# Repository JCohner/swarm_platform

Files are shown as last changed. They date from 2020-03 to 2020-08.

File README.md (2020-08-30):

# Swarm Robotic Platform
### Josh Cohen

## Intro
With the goal of making decentralized, equitable, and sustainable systems, swarm robotic systems seem like a promising framework. Inspired by the success of the open source hardware community over the past 10 years and works like the [swarmbot: Jasmine](http://www.swarmrobot.org/), I hope to attempt to design my own low cost platform that can help propel swarm robotics into the real world. 




## TI CC1310
This is the [micro-conrtoller](http://www.ti.com/product/CC1310) we are using due to its small profile, low power consumption, and integrated RF capabilities. This board is currently interfacing with a [Pololu Zumo](https://www.pololu.com/product/2508) robot through a custom connector board.    

## Current Work
* Working "Firefly Synchronicity" inspired biosynchronicity algorithm that multiplexes time domain such that all robots can communicate within a given time period (\~1 second)
* 2 Working PCB Implementations:
	* Interface to Zumo Robot and CC13310 Launchpad XL
	* From scrath PCB for the CC1310 with working integrated PCB RF Antena that also serves as chassis for a diff drive robot
* Working line following robot that communcites based on the "Bayesian Particle" control laws researched by Ana Pervan and the Murphy lab
	* bit wise state machine to handle state transitions between every encountered intersection

## Directory Structure
* cc1310_code
	code running on the CC1310, controls zumo, implements RF synchronicity algorithm. See directory for more information
* listener
	* code that runs on "Hub" zumo, intercepts all TX'd messages from the zumo cc1310s and interperts the packets to be transmitted on via serial to the host computer, must also be used to communicate to zumos that start|stop them running or change their policies.  
* doc
	documentation relating to the Zumo, CC1310, and other components in this design
* eagle_files
	all PCB related documents
* scripts
	* a script to interpret and graph outputs of the ADC reads from the IR color sensors 
	* small c files in which we can test the bitwise state machine
* interface
	* hub.py is run to open the gui that lets you control the robots and collect data
* stls 
	* holds stl files for which the CAD can be found at [here](https://cad.onshape.com/documents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)

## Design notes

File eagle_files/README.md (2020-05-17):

##Board 2.0
Switched LM1117 voltage regs to constant output, 1 5v reg and one 3.3v output

## Board 1.0
Needs LM1117 to be adjustable

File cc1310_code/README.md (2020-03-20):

# Swarm Robotic Platform
### Josh Cohen

## Intro
With the goal of making decentralized, equitable, and sustainable systems, swarm robotic systems seem like a promising framework. Inspired by the success of the open source hardware community over the past 10 years and works like the [swarmbot: Jasmine](http://www.swarmrobot.org/), I hope to attempt to design my own low cost platform that can help propel swarm robotics into the real world. 

## TI CC1310
This is the [micro-conrtoller](http://www.ti.com/product/CC1310) we are using due to its small profile, low power consumption, and integrated RF capabilities. This board is currently interfacing with a [Pololu Zumo](https://www.pololu.com/product/2508) robot through a custom connector board.    

## Current Work
* Integrate biosynchronicity algorithm with Zumo movement to get them to "dance"
* Iterate on board
	* custom PCB for CC1310
	* LED array for representing bitwise memory
	* power at 3.3V  
* reorganize this github

## Accomplished Work
* Implemented driver library level functionality of control of the Zumo robot
* Designed v1.0 of interface PCB
* Implemented prototype of a custom biosynchronicity algorithm using the CC1310's RF Driver

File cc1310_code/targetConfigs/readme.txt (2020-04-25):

The 'targetConfigs' folder contains target-configuration (.ccxml) files, automatically generated based
on the device and connection settings specified in your project on the Properties > General page.

Please note that in automatic target-configuration management, changes to the project's device and/or
connection settings will either modify an existing or generate a new target-configuration file. Thus,
if you manually edit these auto-generated files, you may need to re-apply your changes. Alternatively,
you may create your own target-configuration file for this project and manage it manually. You can
always switch back to automatic target-configuration management by checking the "Manage the project's
target-configuration automatically" checkbox on the project's Properties > General page.

Josh Additions:
to find serial numbers use the xdsdfu tool found in ~/ti/ccs930/ccs/ccs_base/common/uscif/xds110

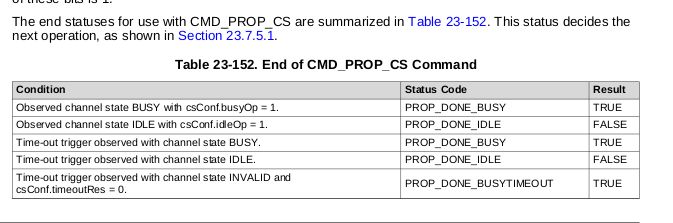
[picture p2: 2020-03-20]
doc/CC1310/RF_CS_return_vals.png

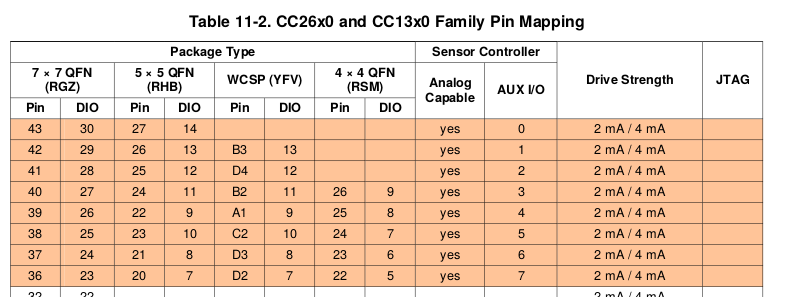
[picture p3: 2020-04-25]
doc/CC1310/helpful_images/IO_Pin__MAP_for_analog.png

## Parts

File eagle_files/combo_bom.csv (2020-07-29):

Part | Vendor | Quantity | Digi-Key Part Number | Customer Reference
10 Pos Male Header | 3M | 25 | 3M9457-10-ND | 10 Pos Male Head
10 Pos Female Header | Sullins Connector Solutions | 10 | S7008-ND | 10 Pos Female Header
8 Pos Female Header | Sullins Connector Solutions | 20 | S7006-ND | 8 Pos Female Header
6 Pos Female Header | Sullins Connector Solutions | 10 | S7004-ND | 6 Pos Female Header
 | Texas Instruments | 10 | LM1117MPX-5.0/NOPBCT-ND | LM1117 5V
 | Texas Instruments | 10 | LM1117MPX-3.3/NOPBCT-ND | LM1117 3v3
 | AVX Corporation | 20 | 478-9320-ND | 10 uF
 | AVX Corporation | 20 | 478-9333-ND | 100 uF
 | Stackpole Electronics Inc | 10 | CF14JT1K00CT-ND | 1k
 | Stackpole Electronics Inc | 50 | CF14JT330RCT-ND | 330
 | Stackpole Electronics Inc | 50 | S200QCT-ND | 220
 | Cree Inc. | 50 | C503B-BCN-CV0Z0462CT-ND | Blue LED
 | Cree Inc. | 50 | C503B-GAN-CB0F0792CT-ND | Green LED

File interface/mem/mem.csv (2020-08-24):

MAC | ser | status
20CE | LDO | 1
A3EB | LXP | 1
C464 | KDS | 1
A171 | M52 | 1
C262 | M4S | 1
A146 | M5X | 1
C683 | M4A | 1
B5A8 | M48 | 1
C219 | M4K | 1
C718 | CGV | 0

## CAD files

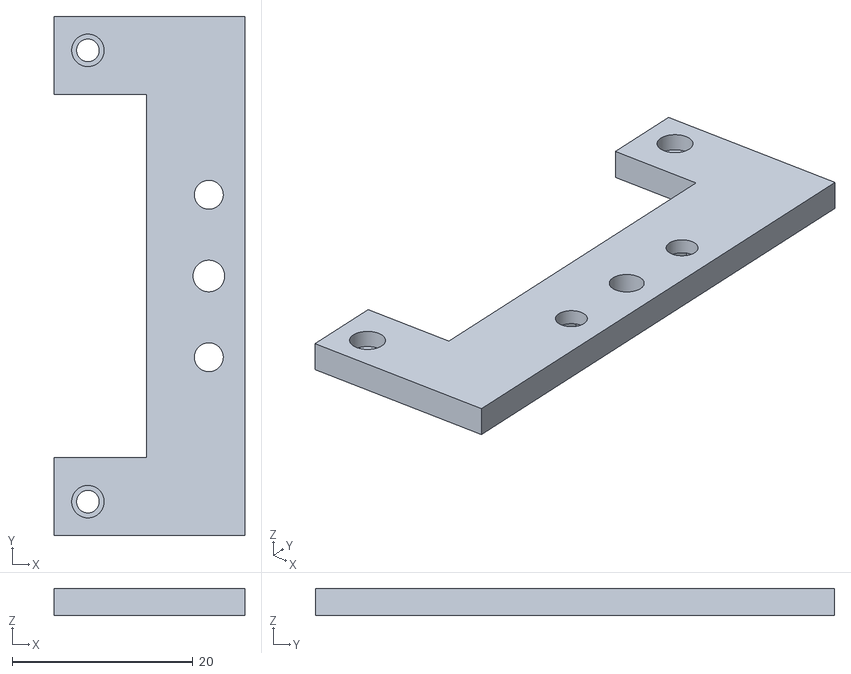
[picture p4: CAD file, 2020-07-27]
stls/front.stl
21.1 x 57.5 x 3.00

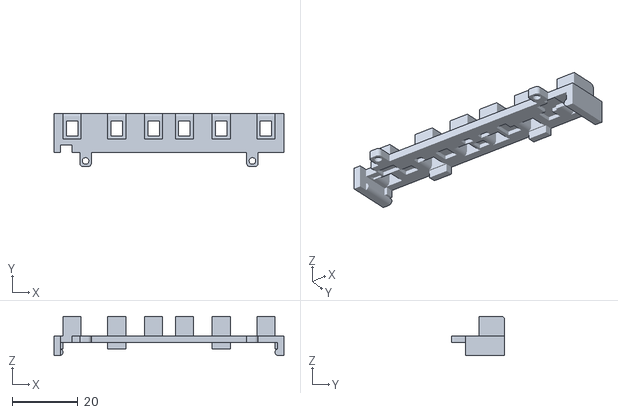
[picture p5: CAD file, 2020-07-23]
stls/shroud.stl
70.0 x 16.2 x 11.9

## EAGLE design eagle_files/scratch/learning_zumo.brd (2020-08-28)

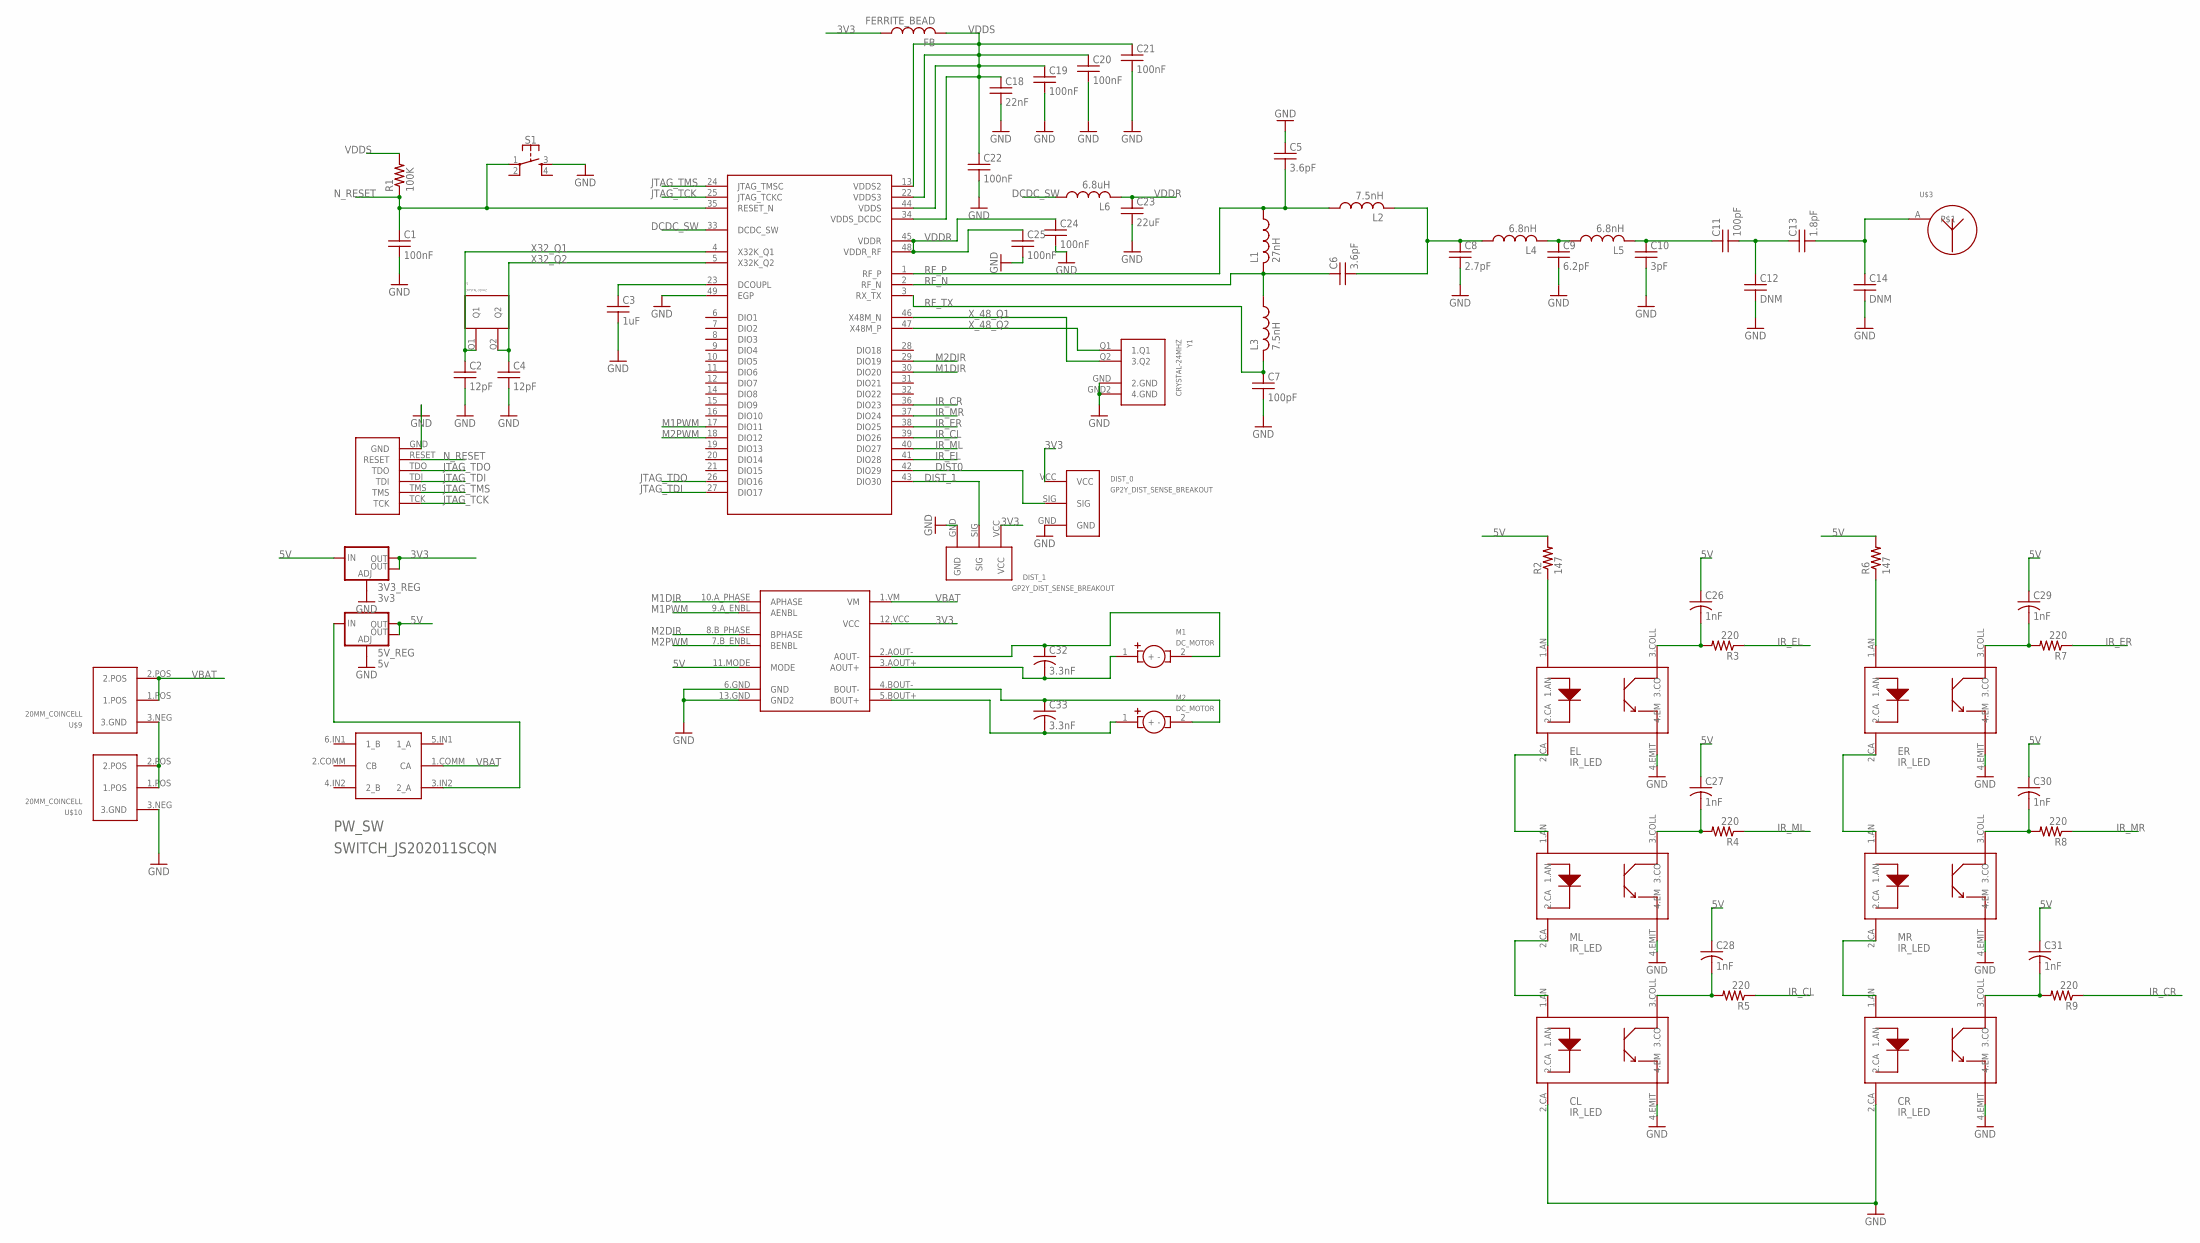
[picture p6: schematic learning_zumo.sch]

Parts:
3V3_REG: 3v3; NU32V7_SOT223
5V_REG: 5v; NU32V7_SOT223
C1, C19, C20, C21, C22, C24, C25: 100nF; C0402_US
C2, C4: 12pF; C0402_US
C3: 1uF; C0402_US
C5, C6: 3.6pF; C0402_US
C7, C11: 100pF; C0402_US
C8: 2.7pF; C0402_US
C9: 6.2pF; C0402_US
C10: 3pF; C0402_US
C12, C14: DNM; C0402_US
C13: 1.8pF; C0402_US
C18: 22nF; C0402_US
C23: 22uF; C0402_US
C26, C27, C28, C29, C30, C31: 1nF; C0805
C32, C33: 3.3nF; C0805
CL: IR_LED
CR: IR_LED
DEBUG_HEADER: DEBUG_BREAKOUT
DIST_0, DIST_1: GP2Y_DIST_SENSE_BREAKOUT; 1X03
DRV8835: DRV8835DRV8835; DRV8835
EL: IR_LED
ER: IR_LED
FB: FERRITE_BEAD
L1: 27nH; L0402_US
L2, L3: 7.5nH; L0402_US
L4, L5: 6.8nH; L0402_US
L6: 6.8uH; R0805
M1, M2: DC_MOTOR; 1X02
ML: IR_LED
MR: IR_LED
PW_SW: SWITCH_JS202011SCQN
R1: 100K; R0402_US
R2, R6: 147; R0805
R3, R4, R5, R7, R8, R9: 220; R0805
S1: MOMENTARY-SWITCH-SPST-2-SMD-4.6X2.8MM; TACTILE_SWITCH_SMD_4.6X2.8MM
U$1: CC1310; QFN50P700X700X100-49N
U$3: ANTENNA
U$9, U$10: 20MM_COINCELL
Y1: CRYSTAL-24MHZ
Y2: CRYSTAL-32KHZ

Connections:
3V3: 3V3_REG.OUTPUT (OUT), 3V3_REG.VOUT (OUT), DIST_0.VCC, DIST_1.VCC, DRV8835.12.VCC (VCC), FB.P$1 (1)
5V: 3V3_REG.INPUT (IN), 5V_REG.OUTPUT (OUT), 5V_REG.VOUT (OUT), C26.1, C27.1, C28.1, C29.1, C30.1, C31.1, DRV8835.11.MODE (MODE), R2.2, R6.2
DCDC_SW: L6.1, U$1.33 (DCDC_SW)
DIST0: DIST_0.SIG, U$1.42 (DIO29)
DIST_1: DIST_1.SIG, U$1.43 (DIO30)
GND: 3V3_REG.GND (ADJ), 5V_REG.GND (ADJ), C1.2, C2.2, C3.2, C4.2, C5.1, C7.2, C8.2, C9.2, C10.2, C12.2, C14.2, C18.2, C19.2, C20.2, C21.2, C22.2, C23.2, C24.2, C25.2, CL.2.CA, CL.4.EMIT (4.EM), CR.2.CA, CR.4.EMIT (4.EM), DEBUG_HEADER.GND, DIST_0.GND, DIST_1.GND, DRV8835.6.GND (GND), DRV8835.13.GND (GND2), EL.4.EMIT (4.EM), ER.4.EMIT (4.EM), ML.4.EMIT (4.EM), MR.4.EMIT (4.EM), S1.3, U$1.49 (EGP), U$10.3.NEG (3.GND), Y1.GND (2.GND), Y1.GND2 (4.GND)
IR_CL: R5.1, U$1.39 (DIO26)
IR_CR: R9.1, U$1.36 (DIO23)
IR_EL: R3.1, U$1.41 (DIO28)
IR_ER: R7.1, U$1.38 (DIO25)
IR_ML: R4.1, U$1.40 (DIO27)
IR_MR: R8.1, U$1.37 (DIO24)
JTAG_TCK: DEBUG_HEADER.TCK, U$1.25 (JTAG_TCKC)
JTAG_TDI: DEBUG_HEADER.TDI, U$1.27 (DIO17)
JTAG_TDO: DEBUG_HEADER.TDO, U$1.26 (DIO16)
JTAG_TMS: DEBUG_HEADER.TMS, U$1.24 (JTAG_TMSC)
M1DIR: DRV8835.10.A_PHASE (APHASE), U$1.30 (DIO20)
M1PWM: DRV8835.9.A_ENBL (AENBL), U$1.17 (DIO11)
M2DIR: DRV8835.8.B_PHASE (BPHASE), U$1.29 (DIO19)
M2PWM: DRV8835.7.B_ENBL (BENBL), U$1.18 (DIO12)
unnamed: C3.1, U$1.23 (DCOUPL)
unnamed: C9.1, L4.P$2 (2), L5.P$1 (1)
unnamed: C10.1, C11.1, L5.P$2 (2)
unnamed: 5V_REG.INPUT (IN), PW_SW.3.IN2 (2_A)
unnamed: U$9.3.NEG (3.GND), U$10.1.POS, U$10.2.POS
unnamed: C11.2, C12.1, C13.1
unnamed: C13.2, C14.1, U$3.A
unnamed: C6.2, C8.1, L2.P$2 (2), L4.P$1 (1)
unnamed: ER.1.AN, R6.1
unnamed: EL.1.AN, R2.1
unnamed: C26.2, EL.3.COLL (3.CO), R3.2
unnamed: EL.2.CA, ML.1.AN
unnamed: CL.1.AN, ML.2.CA
unnamed: C27.2, ML.3.COLL (3.CO), R4.2
unnamed: C33.2, DRV8835.5.BOUT+ (BOUT+), M2.1 (+)
unnamed: C33.1, DRV8835.4.BOUT- (BOUT-), M2.2 (-)
unnamed: C32.2, DRV8835.3.AOUT+ (AOUT+), M1.1 (+)
unnamed: C32.1, DRV8835.2.AOUT- (AOUT-), M1.2 (-)
unnamed: C28.2, CL.3.COLL (3.CO), R5.2
unnamed: C29.2, ER.3.COLL (3.CO), R7.2
unnamed: ER.2.CA, MR.1.AN
unnamed: CR.1.AN, MR.2.CA
unnamed: C30.2, MR.3.COLL (3.CO), R8.2
unnamed: C31.2, CR.3.COLL (3.CO), R9.2
N_RESET: C1.1, DEBUG_HEADER.RESET, R1.P$1 (1), S1.1, U$1.35 (RESET_N)
RF_N: C6.1, L1.P$2 (2), L3.P$1 (1), U$1.2 (RF_N)
RF_P: C5.2, L1.P$1 (1), L2.P$1 (1), U$1.1 (RF_P)
RF_TX: C7.1, L3.P$2 (2), U$1.3 (RX_TX)
VBAT: DRV8835.1.VM (VM), PW_SW.1.COMM (CA), U$9.1.POS, U$9.2.POS
VDDR: C23.1, C24.1, C25.1, L6.2, U$1.45 (VDDR), U$1.48 (VDDR_RF)
VDDS: C18.1, C19.1, C20.1, C21.1, C22.1, FB.P$2 (2), R1.P$2 (2), U$1.13 (VDDS2), U$1.22 (VDDS3), U$1.34 (VDDS_DCDC), U$1.44 (VDDS)
X32_Q1: C2.1, U$1.4 (X32K_Q1), Y2.Q1
X32_Q2: C4.1, U$1.5 (X32K_Q2), Y2.Q2
X_48_Q1: U$1.46 (X48M_N), Y1.Q2 (3.Q2)
X_48_Q2: U$1.47 (X48M_P), Y1.Q1 (1.Q1)

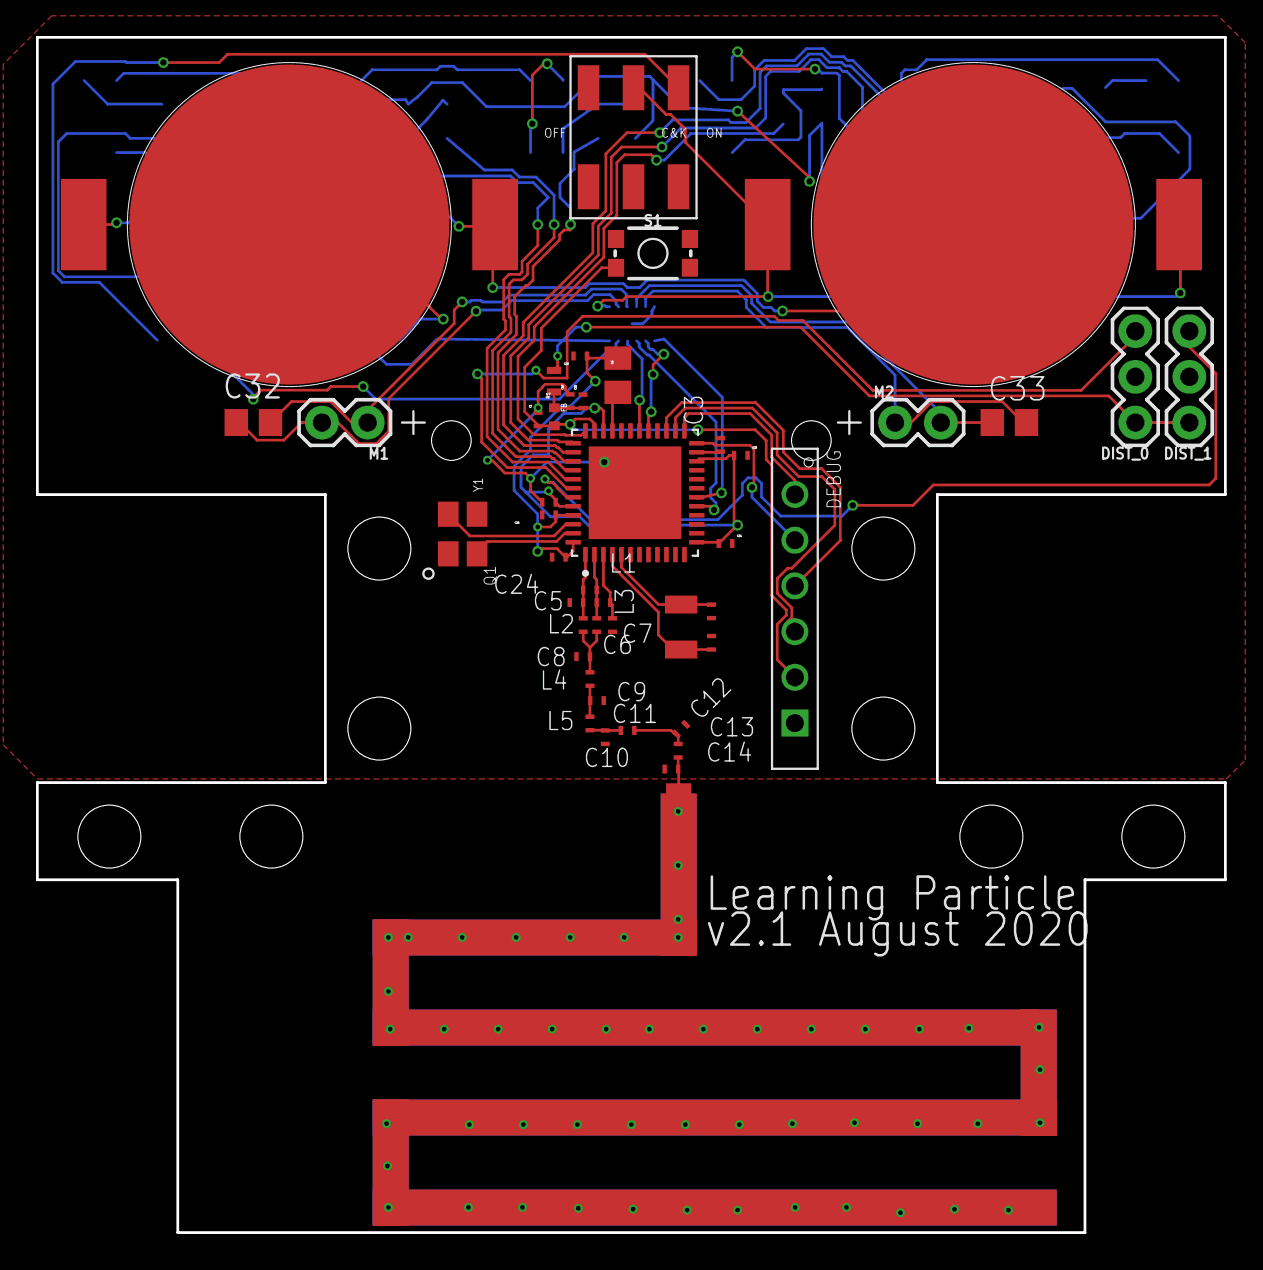
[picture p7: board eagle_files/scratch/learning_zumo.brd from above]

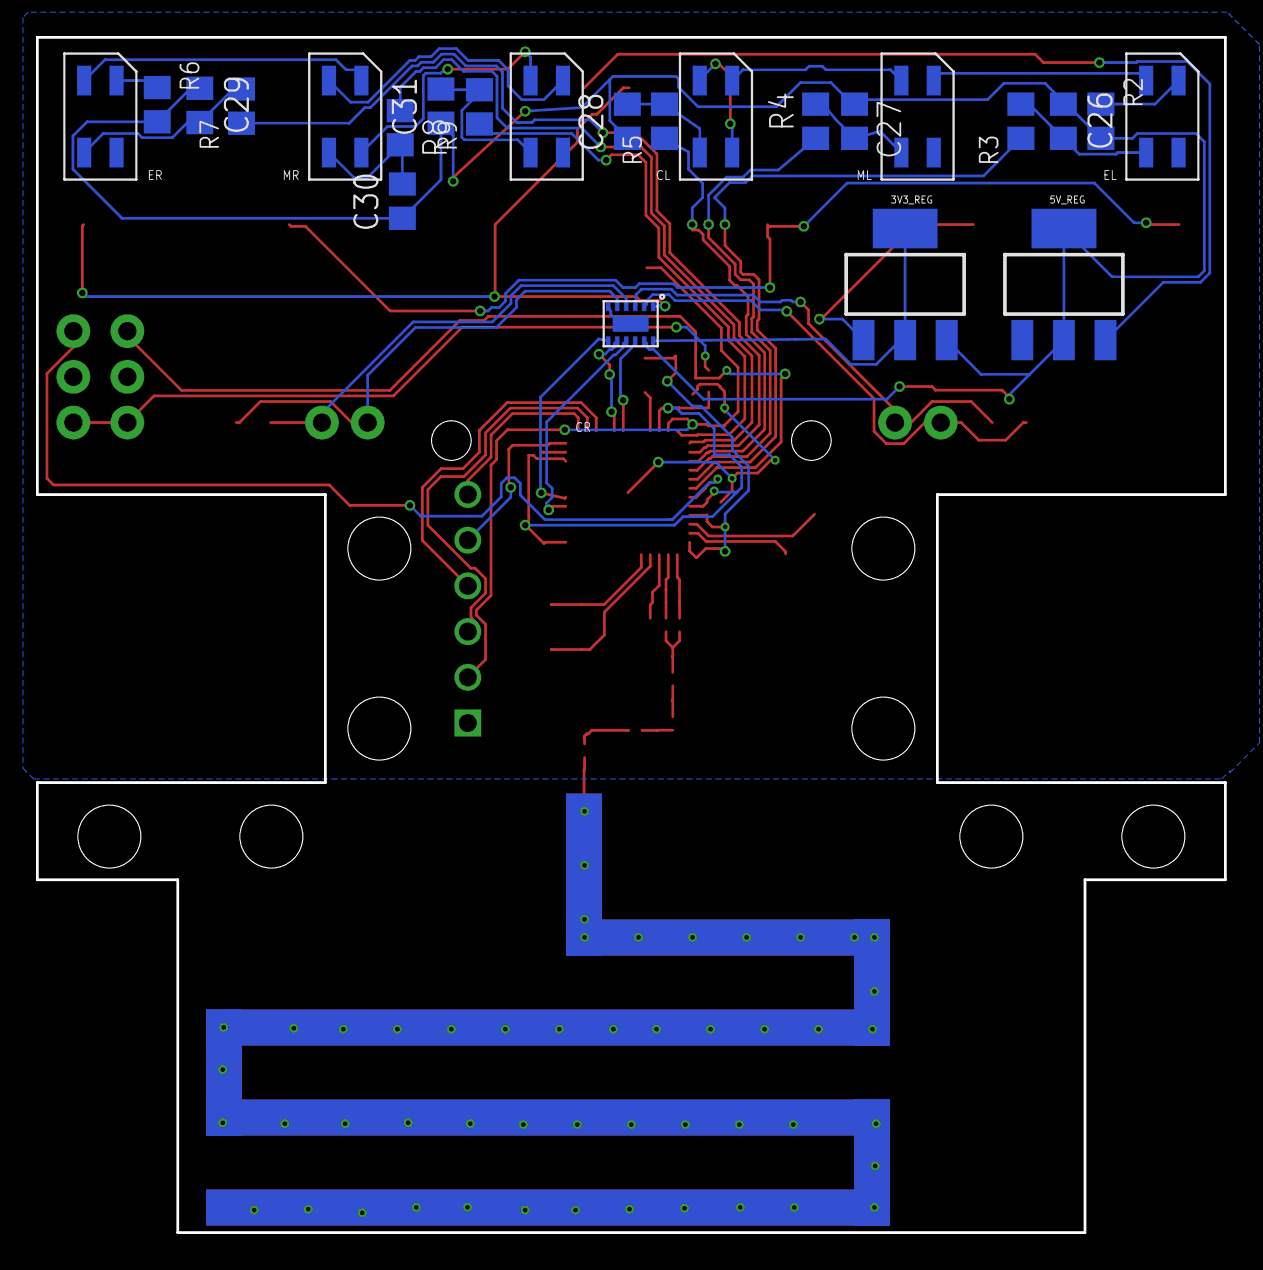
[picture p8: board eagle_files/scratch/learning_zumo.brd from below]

Board: 2 copper layers, 66.0 x 66.4 mm, 68 parts (23 on the bottom side), 55 nets.

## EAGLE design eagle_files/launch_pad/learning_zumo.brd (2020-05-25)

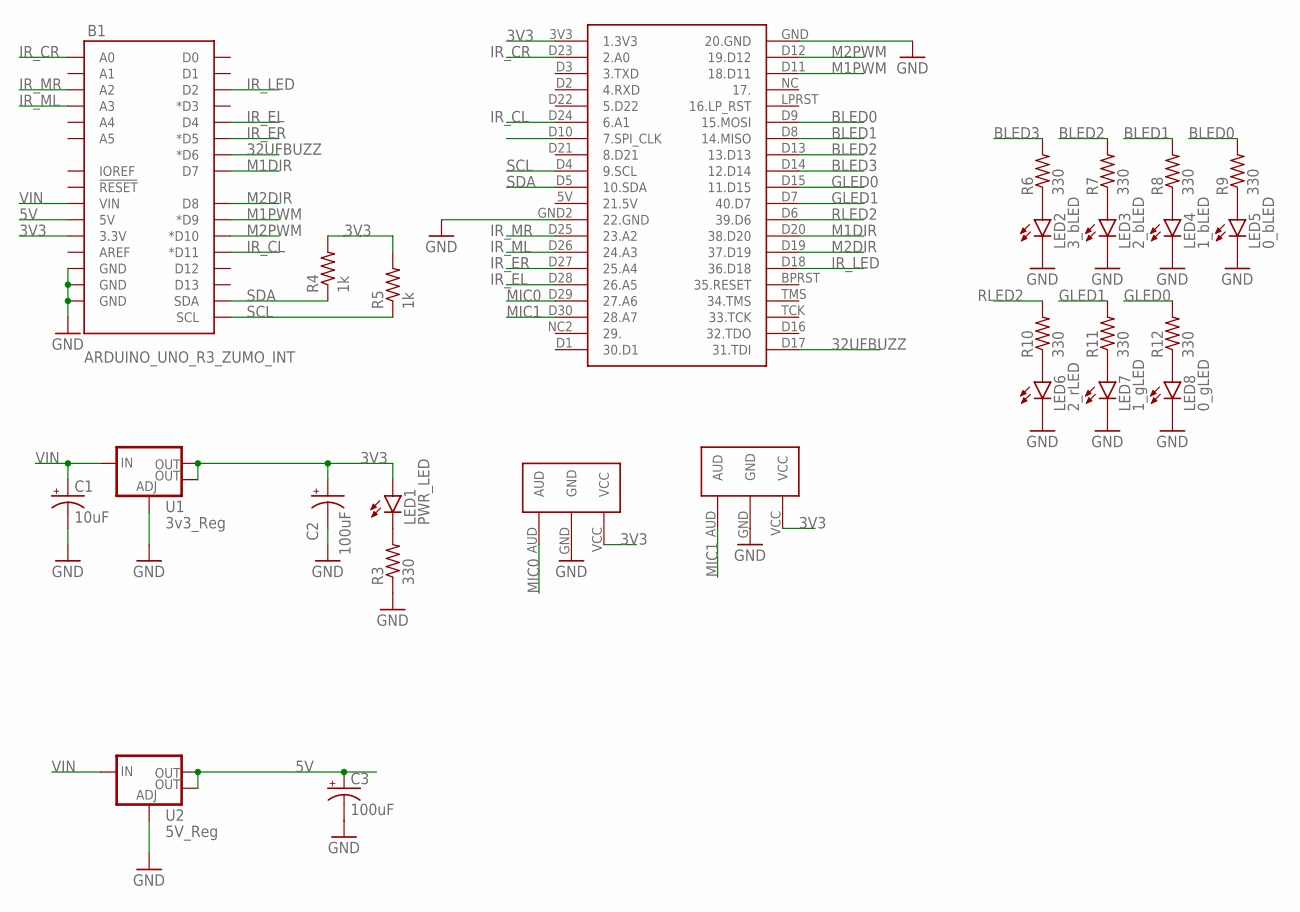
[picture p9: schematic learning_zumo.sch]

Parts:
B1: ARDUINO_UNO_R3_ZUMO_INT; UNO_R3_SHIELD_ICSP
C1: 10uF; E2,5-5
C2, C3: 100uF; E2,5-5
LED1: PWR_LED; LED5MM
LED2: 3_bLED; LED5MM
LED3: 2_bLED; LED5MM
LED4: 1_bLED; LED5MM
LED5: 0_bLED; LED5MM
LED6: 2_rLED; LED5MM
LED7: 1_gLED; LED5MM
LED8: 0_gLED; LED5MM
R3, R6, R7, R8, R9, R10, R11, R12: 330; 0207/10
R4, R5: 1k; 0207/10
U1: 3v3_Reg; NU32V7_SOT223
U2: 5V_Reg; NU32V7_SOT223
U$1: CC1310_INT
U$2, U$3: ANALOG_MIC

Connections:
3V3: B1.3.3V, C2.+, LED1.A, R4.2, R5.2, U1.OUTPUT (OUT), U1.VOUT (OUT), U$1.3V3 (1.3V3), U$2.VCC, U$3.VCC
5V: B1.5V, C3.+, U2.OUTPUT (OUT), U2.VOUT (OUT)
32UFBUZZ: B1.D6 (*D6), U$1.D17 (31.TDI)
BLED0: R9.2, U$1.D9 (15.MOSI)
BLED1: R8.2, U$1.D8 (14.MISO)
BLED2: R7.2, U$1.D13 (13.D13)
BLED3: R6.2, U$1.D14 (12.D14)
GLED0: R12.2, U$1.D15 (11.D15)
GLED1: R11.2, U$1.D7 (40.D7)
GND: B1.GND@0 (GND), B1.GND@1 (GND), B1.GND@2 (GND), C1.-, C2.-, C3.-, LED2.K (C), LED3.K (C), LED4.K (C), LED5.K (C), LED6.K (C), LED7.K (C), LED8.K (C), R3.1, U1.GND (ADJ), U2.GND (ADJ), U$1.GND (20.GND), U$1.GND2 (22.GND), U$2.GND, U$3.GND
IR_CL: B1.D11 (*D11), U$1.D24 (6.A1)
IR_CR: B1.A0, U$1.D23 (2.A0)
IR_EL: B1.D4, U$1.D28 (26.A5)
IR_ER: B1.D5 (*D5), U$1.D27 (25.A4)
IR_LED: B1.D2, U$1.D18 (36.D18)
IR_ML: B1.A3, U$1.D26 (24.A3)
IR_MR: B1.A2, U$1.D25 (23.A2)
M1DIR: B1.D7, U$1.D20 (38.D20)
M1PWM: B1.D9 (*D9), U$1.D11 (18.D11)
M2DIR: B1.D8, U$1.D19 (37.D19)
M2PWM: B1.D10 (*D10), U$1.D12 (19.D12)
MIC0: U$1.D29 (27.A6), U$2.AUD
MIC1: U$1.D30 (28.A7), U$3.AUD
unnamed: LED1.K (C), R3.2
unnamed: LED2.A, R6.1
unnamed: LED3.A, R7.1
unnamed: LED4.A, R8.1
unnamed: LED5.A, R9.1
unnamed: LED6.A, R10.1
unnamed: LED7.A, R11.1
unnamed: LED8.A, R12.1
RLED2: R10.2, U$1.D6 (39.D6)
SCL: B1.SCL, R5.1, U$1.D4 (9.SCL)
SDA: B1.SDA, R4.1, U$1.D5 (10.SDA)
VIN: B1.VIN, C1.+, U1.INPUT (IN), U2.INPUT (IN)

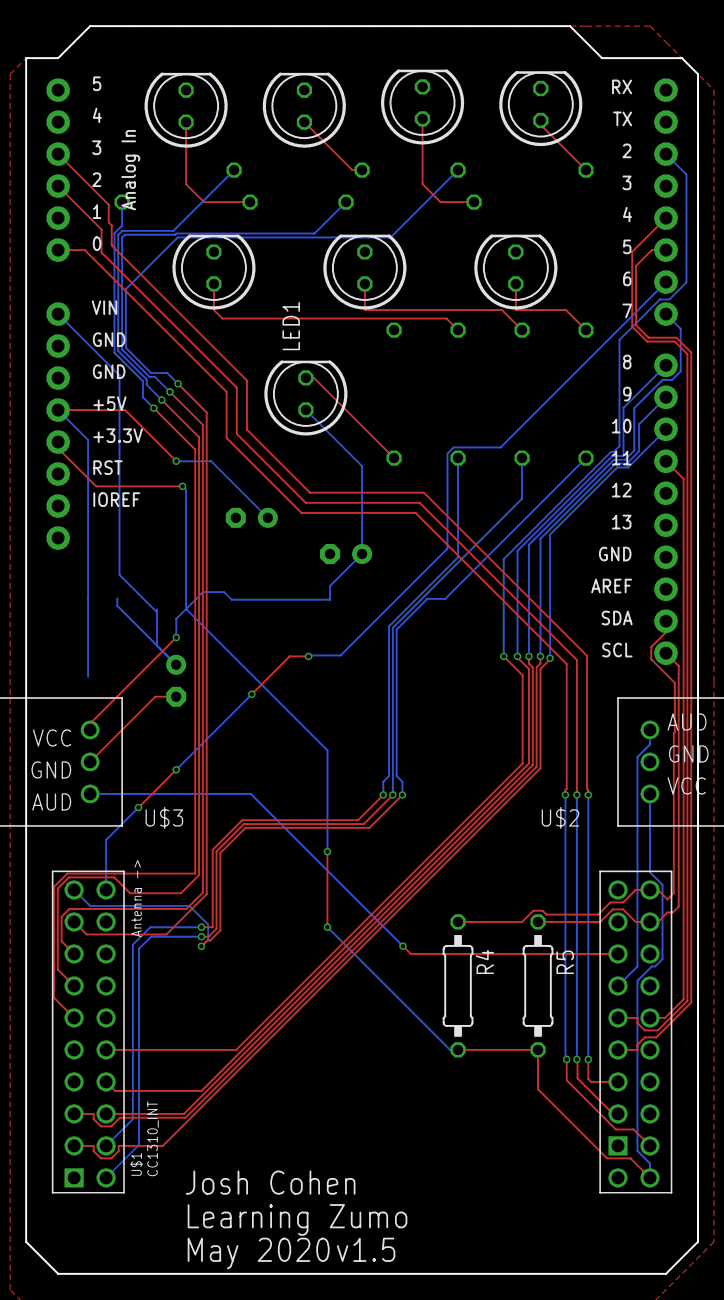
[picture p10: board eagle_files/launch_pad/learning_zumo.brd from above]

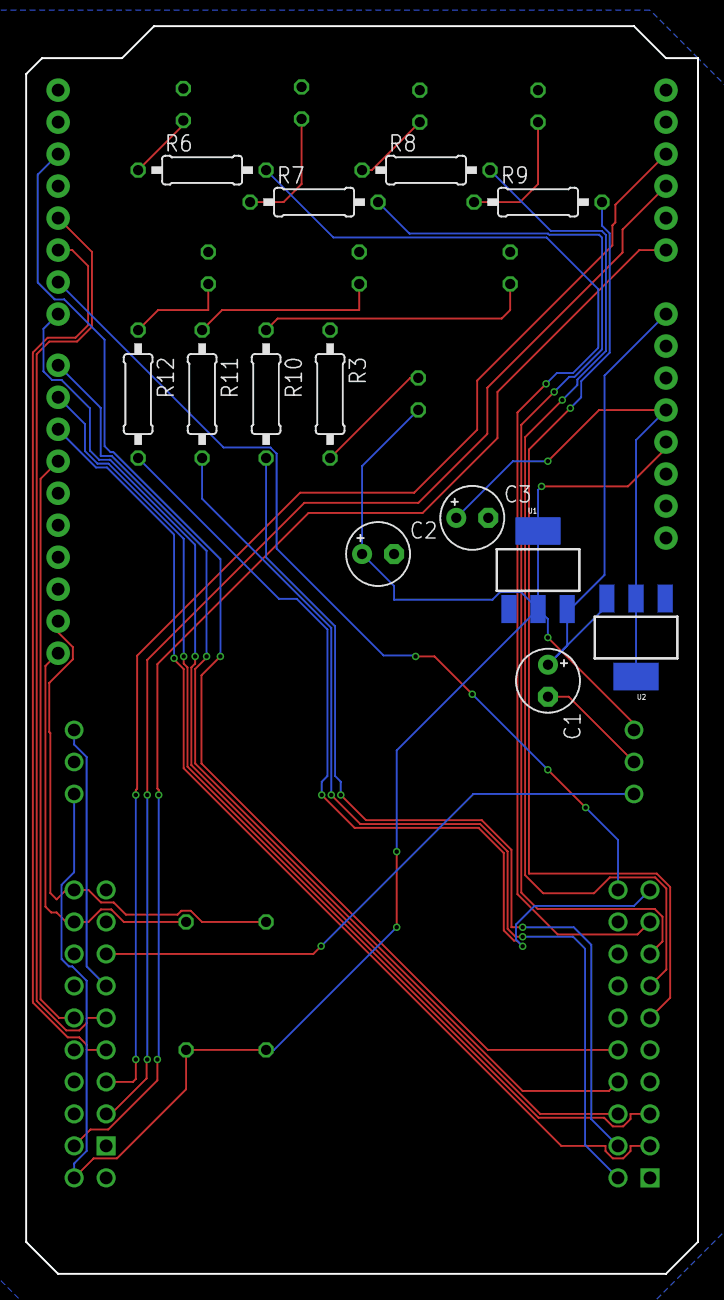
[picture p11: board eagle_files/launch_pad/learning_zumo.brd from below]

Board: 2 copper layers, 53.3 x 99.1 mm, 27 parts (13 on the bottom side), 35 nets.

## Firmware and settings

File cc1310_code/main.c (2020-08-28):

/**
 * @file main.c
 * @brief Main file of the project
 *
 * main's primary use is to perform all necessary initializations.
 * the "main" while loop is also useful for debugging; however, all critical
 * code is executed in timer interrupts.
 */

//CC1310 includes
#include <ccfg.c>
#include <color_track.h>
#include "CC1310_LAUNCHXL.h"
#include <devices/cc13x0/driverlib/prcm.h>
#include <devices/cc13x0/driverlib/sys_ctrl.h>
//developed includes
#include "imu.h"
#include "gpio.h"
#include "i2c_accel.h"
#include "i2c_gyro.h"
#include "pwm.h"
#include "zumo.h"
#include "zumo_rf.h"
#include "adc.h"
#include "helpful.h"
#include "ir_sense.h"
#include "zumo_moves.h"
#include "interrupt_timer.h"
#include "comm_packet.h"
#include "dist_sense.h"
#include "leds.h"
#include "rando.h"

static char buffer[60];

uint8_t pol;
uint8_t pol_lookup()
{

    uint16_t mach_id = get_mach_id();
    switch(mach_id)
    {
    case 0xC464:
        pol = 0;
        break;
    case 0xC219:
        pol = 0;
        break;
    case 0xA171:
        pol = 2;
        break;
    case 0xC683:
        pol = 2;
        break;
    case 0x20CE:
        pol = 3;
        break;
    case 0xB5A8:
        pol = 3;
        break;
    case 0xC262:
        pol = 1;
        break;
    case 0xA3EB:
        pol = 1;
        break;
    case 0xC718:
        pol = 0;
        break;
    default:
        sprintf(buffer, "no match for %X\r\n", mach_id);
        WriteUART0(buffer);
        while(1);
    }

    return pol;
}



uint32_t adc_vals[8];
uint32_t adc_ave_vals[8];
int main(void)
{
    //CC1310 Requires you specifically turn on any peripheral you are going to use
    PRCMPowerDomainOn(PRCM_DOMAIN_PERIPH | PRCM_DOMAIN_SERIAL | PRCM_DOMAIN_RFCORE);
    while (PRCMPowerDomainStatus(PRCM_DOMAIN_PERIPH | PRCM_DOMAIN_SERIAL | PRCM_DOMAIN_RFCORE)
    != PRCM_DOMAIN_POWER_ON);

    //from imu.c: begins uart and i2c; performs accelerometer and gyro setup
    start();
    //opens digital input output pins, and analog output pins configures motor driver specific pins
    InitGPIO();
    PWMEnable(); //sets timers to finish configuring analog out pins
    //initialize analog input
    InitADC();
    //initialize True Random Number Gen periph
    RandoConfig();
    //initializes polict and sets machine ID to first 2 bytes of MAC address



    set_mach_id(HWREG(FCFG1_BASE +0x2F0) & 0xFFFF);
    //configures rf driver, configures application specific packages, makes initial chirp call
    rf_setup();
    //explicitly starts motors in off state
    setMotor(M2, 0, 0);
    setMotor(M1, 0, 0);
    //usefull delay on startup (also seems needed for random number gen??)
    delay(1);

    //IF WE WANT RAND POLICY
//    set_policy(get_random_num(4));

    set_policy(pol_lookup());

//    sprintf(buffer, "rand: %u\r\n" ,get_policy());
//    WriteUART0(buffer);
//    while(1);
    //start up neccesarries for ir sensing (GPT2A full width set up)
    IR_SenseSetup();
    //configures GPIOs associated with LEDs
    setup_leds();

    //sets open loop control characteristics
    set_on_time(400);
    set_offset_time(500);

    /*
     * State Track Initialization for Circulatory Map
     * exclusively comment this in for state machine
     * to be in circulatory map configuration
     * */
//    uint8_t bbs[2] = {3,4};
//    init_state(0b1100, 2, bbs, 4, 1, 0, 0x7);

    /*
     * State Track Initialization for 5 node map
     * exclusively comment this in for state machine
     * to be in 5 node map configuration
     * */
      uint8_t bbs[1] = {3};
      init_state(0b110, 1, bbs, 3, 0, 0, 0x3);

      //Enable timer based interrupts:
      //    GPT1A - Openloop motor control
      //    GPT1B - Information sensing and decision making
      //    GPT3A - RF Communication
      InterTimerEnable();

      while(1)
      {
//          uint32_t forw = ReadDistForward();
//          uint32_t side = ReadDist45();
//          sprintf(buffer, "%u %u\r\n", forw, side);
//          WriteUART0(buffer);



          ReadIR(adc_vals);
////          WriteRF(adc_vals);
                    sprintf(buffer,"%u, %u, %u, %u, %u, %u\r\n", adc_vals[5], adc_vals[3], adc_vals[1],
                                      adc_vals[0], adc_vals[2], adc_vals[4]);
                    WriteUART0(buffer);


//          sprintf(buffer,"dist val %u\r\n", ReadDist());
//          WriteUART0(buffer);
//          GPIO_toggleDio(CC1310_LAUNCHXL_PIN_GLED);
//          read_imu();
      }


	return 0;
}

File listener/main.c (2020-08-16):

/**
 * main.c
 */
#include <ccfg.c>
#include "CC1310_LAUNCHXL.h"

#include <devices/cc13x0/driverlib/prcm.h>
#include <devices/cc13x0/driverlib/uart.h>
#include <devices/cc13x0/driverlib/sys_ctrl.h>
#include "rf_listener.h"
#include <stdlib.h>

#include "gpio.h"
#include "uart.h"
#include "print_info.h"
#include "leds.h"
#include "helpful.h"

static char buffer[50];
int main(void)
{

    PRCMPowerDomainOn(PRCM_DOMAIN_PERIPH | PRCM_DOMAIN_SERIAL | PRCM_DOMAIN_RFCORE);
    while (PRCMPowerDomainStatus(PRCM_DOMAIN_PERIPH | PRCM_DOMAIN_SERIAL | PRCM_DOMAIN_RFCORE)
    != PRCM_DOMAIN_POWER_ON);

    InitGPIO();
    GPIO_setDio(CC1310_LAUNCHXL_PIN_GLED);

    InitUART0();
    rf_setup();
    GPIO_toggleDio(CC1310_LAUNCHXL_PIN_RLED);
    WriteUART0("got here\r\n");


    READUART0_AS_ENABLE();

    setup_leds();

      while(1)
      {
//          GPIO_setDio(CC1310_LAUNCHXL_PIN_RLED);

          uint8_t flag = ReadUART0_AS(buffer, 16);
          if (flag)
          {
              char * pEnd;
              rf_post_message((uint32_t) strtoul(buffer, &pEnd, 16));
          }
          rf_main();

      }


	return 0;
}

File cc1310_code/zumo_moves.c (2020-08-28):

/*
 * zumo_moves.c
 *
 *  Created on: Jun 21, 2020
 *      Author: jambox
 */
#include "zumo_moves.h"
#include "gpio.h"
#include "uart.h"

static uint32_t on_time = 0;
static uint16_t reset_time = 0;

static uint16_t offset_time = 0;
static volatile uint32_t counter = 0;
static volatile uint8_t state = 0;

void setMotor(int motor, int dir, int value)
{
    int DIR_pin, PWM_pin;
    if (motor == M1)
    {
       DIR_pin = M1_DIR;
       PWM_pin = M1_PWM;
    }
    else if (motor == M2)
    {
        DIR_pin = M2_DIR;
        PWM_pin = M2_PWM;
    }

    int set_val = 1022 - value;
    if (set_val < 0){
        set_val = 0;
    }

//    if (value < 0)
//    {
//        dir = !dir;
//    }

    GPIO_writeDio(DIR_pin, dir);
    PWMSet(PWM_pin, set_val);
}



void init_openloop(void)
{
    state = 1;
    counter = 0;
    set_actuation_flag(1);
    set_actuation_pre_ret_flag(1);
    WriteUART0("loop initialized\r\n");
}

void end_openloop(void)
{
    GPIO_toggleDio(BLED0);
    state = 0;
}

void set_on_time(uint32_t counts)
{
    on_time = counts;
}

void set_counts(uint32_t counts)
{
    counter = counts;
}


void set_offset_time(uint32_t counts)
{
    offset_time = counts;
}

void set_reset_time(uint32_t counts)
{
    reset_time = counts;
}

char buffer[50];

//0 - CCW (left)
//1 - CW (right)
void rotate(int dir)
{
    //ensures all non zero inputs normalized to 1
    if (dir)
    {
        dir = 1;
//        WriteUART0("turning CW\r\n");
    }
    else
    {
//        WriteUART0("turning CounterCW\r\n");
        ;
    }

    setMotor(M1, dir, MOTOR_TURN);
    setMotor(M2, !dir, MOTOR_TURN);
}

//0 - CCW (left)
//1 - CW (right)
void steer(int dir)
{
    if (dir)
    {
        setMotor(M1, 0, MOTOR_ON - 50);
        setMotor(M2, 0, MOTOR_ON + 50);
    }
    else
    {
        setMotor(M1, 0, MOTOR_ON + 50);
        setMotor(M2, 0, MOTOR_ON - 50);
    }
}

//TODO for scalibility can definitely reference (bb - 1) value for number of
//      bits to bitshift
uint8_t mask_policy(uint8_t policy)
{
    uint8_t ret;
    uint8_t idx = get_bb_idx();
    if (idx == 0)
    {
        ret = policy & get_mask();
    }
    else if (idx == 1)
    {
        ret = (policy & (get_mask() << 2)) >> 2;
    }

    return ret;
}

/*!
 *  \brief Called at 1kHz, if state is active will take over controlling
 *      motors and open loop turn the robot. Uses state as a mask to get policy bit OR
 *      return_policy bit relevant to current intersection
 */

void openloop_turn()
{

//    sprintf(buffer, "tot count: %u, offset: %u\r\n", total_count, timer_offset);
//    WriteUART0(buffer);
//    while(1);

    uint8_t xc_state = get_xc_state();
    uint8_t policy= get_policy();
    uint8_t ret_policy = get_return_policy();

    //this gets the single bit rotation value we need
    //this works due to the OHE nature of the xc_state representation
    uint8_t dir;
    if (!get_return_flag())
    {
        dir = xc_state & mask_policy(policy);
    }
    else
    {
        dir = xc_state & mask_policy(ret_policy);
    }
    //it is recommended that clearing the interrupt flag is not the last command
    TimerIntClear(GPT1_BASE, TIMER_TIMA_TIMEOUT);
    if (state && counter < (on_time + offset_time))
    {
        if (counter > offset_time)
        {
//            WriteUART0("ACTUATING\r\n");
            sprintf(buffer, "dir: %u\r\n", dir);
            WriteUART0(buffer);
            rotate(dir);
        }
        else
        {
            //drive forward cautiously
            setMotor(M1, 0, MOTOR_ON);
            setMotor(M2, 0, MOTOR_ON);
        }

        counter++;
//        sprintf(buffer, "counter %u\r\n", counter);
//        WriteUART0(buffer);
    }
    else if (counter >= on_time + offset_time && state)
    {

//        GPIO_toggleDio(BLED0);
        setMotor(M1, dir, MOTOR_OFF);
        setMotor(M2, !dir, MOTOR_OFF);
//        delay(5);
        end_openloop();
        set_actuation_flag(0);
        state = 0;
    }



//    if(state)
//    {
//        WriteUART0("hi\r\n");
//    }

    return;
}

/*!
 *  \brief calls flag getters from StateTrack, calls open loop controller to turn
 *      if state change detected
 *
 */
void manage_intersection()
{
    uint8_t xc_state = get_xc_state();
    uint8_t prev_xc_state=  get_prev_xc_state();

//    sprintf(buffer, "prev: %u, cur: %u\r\n",prev_xc_state, xc_state);
//    WriteUART0(buffer);
    if (xc_state != prev_xc_state)
    {
        GPIO_toggleDio(BLED3);
        init_openloop();
    }

    set_prev_xc_state(xc_state);
    set_intersection_flag(0);
    return;
}

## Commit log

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2020-02-29 fixed broken i2c send
    [i2c_accel.c, i2c_gyro.c, i2c_master.c]
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2020-03-01 initializing 2 pwm outputs and made function to set value
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2020-03-17 close to working? have a queue overflow error that occurs occaisonally
    [zumo_rf.c]
2020-03-18 fixed queue filling issue
    [zumo_rf.c]
2020-03-19 inital board and schematic files for interface board
    [zumo_cc.brd, zumo_cc.sch]
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2020-03-31 most advanced implementation yet, going to implement filtering based on averging next
2020-03-31 prototype of avergaing filter for 10 most recent time deltas
2020-04-01 caught int division bug
    [zumo_rf.c]
2020-04-07 added UART wait for input step function to make debugging easier
2020-04-14 liiited quickest switching tim to improve performance, non averaged imp working robustly
2020-04-19 got a singleshot adc pin read working, the READADC() function doesnt quite work yet, but the singular read in init does
2020-04-26 fixed silly bug in adc variable declaration
    [main.c]
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2020-04-26 added funcitonality to turn adc readings into useful ir sensor data aqs
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2020-05-10 this is now the low level driver for adc reads, ir interfacing data read interp handled by ir_sense middleware now
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2020-05-17 increased output buffer size to dump more info via uart, also stashing commit because going to debug on new board
2020-05-17 minor power side revision, using fixedoutput versions of l1117 from now on, wont need any voltage but 3v3 and 5v can spare the 4 resistors and simplify board
    [learning_zumo.brd, learning_zumo.sch]
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2020-05-25 further tuning control algo, fixed missed revision bug
    [zumo.c, zumo.h]
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2020-05-25 reflects most recent pcb changes
    [learning_zumo.brd, learning_zumo.sch]
2020-05-28 found bug in averaging
    [zumo_rf.c]
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2020-06-07 tuned detection thresholds, broke out detecting poi into its own function
    [zumo.c, zumo.h]
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2020-06-07 added mechanism to limit rate of uart printing without limiting actual proc rate
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2020-06-08 1st implementation of py serial script, using to prototype barcode stuff rn
2020-06-09 stashing last of barcode, switching to a more state machine based interp
2020-06-10 going to clean up and refine poi detect. good proto framework though
    [zumo_cc.brd, zumo_cc.sch]
2020-06-23 this is now low level motor driver, also has functions for commanding open loop efforts
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2020-06-24 moved open loop control and execute polic logic here, implemented rotate function that calls motor actuation, added time based offset to openloop turn
2020-06-24 changing state transition schema, no longer based on handedness, also renamed some state variables for clarity, next step is only performing xc_state transitions in state track file
    [color_track.c, main.c, zumo.c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]
2020-06-26 latest line following, decision making code. pretty well refined, will revisit when we have better wireless testing infrastructure
2020-06-26 listnening hub that will print all RF messages to serial on computer for visualization
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2020-07-01 increased base movement speed, broke out rotation function for general use
    [zumo.h]
2020-07-02 replaced bias flag with actuation flag because they accomplish the same thing, cleared up language in zumo_moves
    [zumo.c, zumo_moves.c]
2020-07-02 pivoting away from current offset based open loop control as it is messy, will try get robot to notice intersections
2020-07-04 cleaned up dependecies, reverted drive line back to more elegant solution
    [zumo.c, zumo.h]
2020-07-04 added manage intersection to simplify and replace 'execute_policy()'
    [zumo_moves.c]
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2020-07-10 refining communication paradigm to better facillitate multi bot communication, reintroducing CS capacities
2020-07-13 fine tuning and code cleanup, performance is great. improvements from here on out will involve adding info to the map for error catching
    [color_track.c]
2020-07-13 didnt realize i was double utilizing TIMER1, now using TIMER2 for this (man that bug took a long time to find)
    [helpful.c]
2020-07-13 ironed out last bugs that would let me use this at 1.27ms period
    [interrupt_timer.c]
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2020-07-15 small change to prevent mixing up target detection with other poi detection
    [color_track.c]
2020-07-15 fixed silly bug introduced by swithcing from RxSniff to plain RX
    [zumo_rf.c]
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2020-07-15 cleanup, more work still be done in terms of moving items out of mainloop and structuring heirarchy of interrupts such that everything is running at determined rate
2020-07-17 newest from scratch pcb design
    [learning_zumo.brd, learning_zumo.sch]
2020-07-18 refined newest board design, adding debugger pinout locals
    [learning_zumo.sch]
2020-07-19 days worth of work, added a bunch of componenets to the libraries, gave the power considerations a first take, began implementing the board, implement motor driver circuitry
    [learning_zumo.brd, learning_zumo.sch]
2020-07-19 begining to account for materials adn costs
    [bom.csv]
2020-07-22 all components now speced out and priced on bom
    [bom.csv]
2020-07-22 figuring last details on antenna balun
    [learning_zumo.brd, learning_zumo.sch]
2020-07-22 most updated, finished balun and other minimum reqs for CC1310, working on integrating battery motor driver and sensors
    [learning_zumo.brd, learning_zumo.sch]
2020-07-22 finished up iteration 1 of the board!
    [learning_zumo.brd, learning_zumo.sch]
2020-07-23 updated bom, lbr, and epf to reflect semi completion of v2.0
    [bom.csv]
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2020-07-23 finialized board pre submitting, added vias between top and bottom trace of antenna
    [learning_zumo.brd, learning_zumo.sch, shroud.stl]
2020-07-23 added better logic to check near, it is a little opaque, but should be discernable if you track the bitwise operators
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2020-07-24 now incorporating analog forward distance to nearest signal in drive line such that the bot slows down as it approaches an obstacle. possible TODO: add some priority system, as documented in code thi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
    [zumo.c, zumo.h]
2020-07-27 stl for the distance sensor mount
    [front.stl]
2020-07-29 huge rework of state incrementation, defined a bitwise state machine that iterates through COHE (circular one hot encoding, specialized encoding mechanism for circular based binary search flow), adde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
2020-07-29 changed our open loop function such that it can perform the correct masking and bitwise operations on the policy (with the newly expanded state and policy), added a helper to aid in this
    [zumo_moves.c]
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2020-07-29 bom for v1.75 and v2.0 boards
    [bom.csv, combo_bom.csv]
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2020-08-06 using async uart to act as listner hub but also send commands to our friends (fellow swarm bots)
2020-08-07 2 main features: added ability to switch to new policy sent from hub
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2020-08-11 fixed up some silliniess, now properly splitting the timer (GPT1) into Timer_A and Timer_B using timerA for motor control, timerB for fixed rate actuation of radio
    [interrupt_timer.c]
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2020-08-11 moving from scripts to here, this will be the desktop interface into interacting with the swarm and deserves to be at the top level
    [mem.csv]
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2020-08-11 big change where we moved all sensing and driving commands to an interrupt timer
2020-08-12 added classful nature
    [mem.csv]
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2020-08-12 fixed small bug re: leds lighting
    [main.c]
2020-08-13 caught bug of sender id in comm packet being 8 bit instead of newly expanded 16 bit
    [comm_packet.c]
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2020-08-13 building out modularity of state machine system such that it is easy to switch between two map designs
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2020-08-16 found insidious bug, used strtol instead of strtoul, which lead to truncation of full 32 bit entries to the 2s compliment format (present in IDs with first char being > 7)
    [main.c]
2020-08-16 messing around with timings. might have to reduce driving timer by 1/2 if issues arise, increased rf timer by 2x as well
    [interrupt_timer.c]
2020-08-17 critical threshold change for driving on the black as printed by quarter copies
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2020-08-18 implemented random offset to sync to avoid collisions
    [zumo_rf.c]
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2020-08-22 broke out side distance sensor
2020-08-22 caught bug where we were incorrectly writing successful neighbor policy (due to chaning packet struct)
    [comm_packet.c]
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2020-08-22 added doyxgen style (and general) comments, randomizedd starting policy, added some debug prints to main loop
2020-08-22 slightly altered min and max idle times, commented out some debug prints
2020-08-23 made code threadful such that we could read and write from serial port
2020-08-24 updated mem formating
    [mem.csv]
2020-08-24 rework of 'check_near' function that ensured only robots on the same segment could communicate
    [comm_packet.c]
2020-08-26 added code to prevent false detects of target when stopped at intersection, turned off LEDs for debugging
    [color_track.c]
2020-08-26 added check distance function (not in use in this iteration) that will reverse if too close, right now functionality just stops the robot when it is too close
    [zumo.c, zumo.h]
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2020-08-28 latest WORKING version of board and schematic
    [learning_zumo.brd, learning_zumo.sch]
2020-08-28 added another return flag, currently non functional but may enable more reliable state machine behavior
2020-08-28 broke out led functionality to middle ware
